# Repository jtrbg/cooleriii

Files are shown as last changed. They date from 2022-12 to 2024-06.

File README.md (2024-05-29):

# cooler iii

An application that is used to control the CoolerCoolerCooler

## Current Issues
1. **Weight**
   - The weight of the current prototype is too heavy for the current motor (even without a loaded cooler). The motor and/or overall weight of the build needs to be optimized.

2. **Precision and Strength of Printed Parts**
   - While the printed motor hub connecting the wheel and the motors originally broke from the stress (`orig_motor_hub.stl`), the new design does not break, but the mounting holes bend causing tilt in the wheels (`new_motor_hub.stl`).

3. **Functionality**
   - **Axis Module:** Did not provide accurate readings of direction even when tilt was disregarded (level surface).
   - **Bluetooth and Application:** While the custom application could read from the module, it would not 'write' proper instructions to the device. With that, we were able to determine the location of both the phone and the device, but unable to properly communicate/decode instructions from the app.

## GUIDE TO USE
## Main Application

The main app features two screens which the user can swipe between 
- Automatic Screen
  - This screen features a map that pins both the user's location and the cooler's location 
  - When viewing this screen, control mode will be set to automatic, allowing the cooler to follow the user
- Manual Screen
  - This screen features a controller UI that is customizable in settings
  - When viewing this screen, control mode will be set to manual, allowing the user to control the cooler
If the app has not been bonded, the user will be prompted to scan and connect to a 
CoolerCoolerCooler BT module   (OnStartup)

## Bluetooth Connectivity

To connect to the BT module of the cooler, the user will be directed to the Bluetooth Screen which
allows the user to scan, connect, and bond the cooler's BT module to the app
- Bluetooth Screen
  - This screen contains the information of the currently bonded device and an expandable menu that scans for devices
  - If a device is not connected, the app will automatically scan for new devices
  - To connect to a device, the user will simply tap on a desired device's label

## Automatic pathfinding

When a user is on the Automatic Screen and the 'Follow-Me' toggle is switched on, the cooler follows
the user's GPS signal using a determined pathfinding algorithm to navigate unseen obstacles

## Controller UI

To manually control the cooler, the user can swipe or tap to the Manual Screen and use the
wheel and slider buttons to control the coolers direction and speed

## Settings - Customizations/Modifications

Any customizations/modifications to the app or controls will be found through the settings button
at the top right of the Main Screen
- Theme
- Controller
- GPS
- Bluetooth
- Cooler

### Dependencies

- flutter_blue_plus ^1.3.1
  - startLeScan(UUID[],LeScanCallback) has been deprecated
  - stopLeScan(LeScanCallback) has been deprecated
- location ^4.4.0
  - isFromMockProvider() has been deprecated
- settings_ui ^2.0.2      (PLAN TO REMOVE)

### Permissions(On phone)

- Bluetooth
- Location
- Read and Write

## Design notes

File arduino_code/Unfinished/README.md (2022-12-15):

This folder contains code that was used to test modules and an attempt to create a serial connection to the device

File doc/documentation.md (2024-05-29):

```markdown
# Cooler Cooler Cooler Documentation

### Matthew Demchuk, Joshua Brull, Jovanni Rodriguez, Kai Xu
#### Dr. Franchi
#### COSC 451
#### Fall 2022

## Original Concept
**FollowMeCooler**  
We wanted to expand upon their idea and make it more successful in two areas: responsiveness and being able to drive the cooler on the beach (offroading).

## Chassis Design

### Materials
- ½ in x 2 ft x 4 ft Sanded Plywood
- 1-½ in x ⅝ in Inside Corner Braces
- 8 x 1-½ in Wood Screws
- 9 in Balloon Beach Wheels
- 12V 12 rpm DC Worm Gear Motor
- 8 in Caster Wheel
- ⅜ in x 1-½ in Bolts
- ⅜ in Lock Nuts
- ⅜ in Washers
- M4 x 15mm Steel Bolts
- Tupperware
- Cooler

### Dimensions
- Main Body: 14-⅛ in x 10-⅞ in x 4 in
- Caster Wheel Plate: 9-½ in x 9-⅛ in x ½ in
- Motor Mount Plates: 2-¼ in x 2 in x ½ in

### Details
- Corner Braces used on both the Motor Mount and Caster Wheel plates to help secure them to the Main Body. Though one of the Motor Mount plates corner braces screws are stripped causing it to tilt when placed on the ground.
- M4 Bolts are used to attach the Motor to the Motor Mount Plate.
- ⅜ in Bolts, Lock Nuts, and Washers used to mount the Caster Wheel to the Caster Wheel Mount Plate.
- Corner Brace Screws are sticking out in the Main Body will need to sanded down or cut off to prevent user injury.
- Both Plates will need to be redesigned if the motor or caster wheel is changed in the future.

## 3-D Motor Mount

With the current motor and wheels for the robot, the 3-D model does need to be modified. Both the bolt’s and motor shaft do not fit the holes on the mount and have required us to drill them out a bit to fit properly. These will need to be adjusted to fit both the wheel and motor properly.

## Wire Diagram

This is how the robot is currently wired up and allows the ArduinoBlue app to connect to the device. This does need to be improved as it is currently believed that there is too much power running into the Breadboard overloading the HM-10 if it is the only thing that is plugged into the board. From our understanding resistors were needed to prevent this from happening but were unable to figure out how to properly accomplish that in the device.

## Parts List
- 2 - 9” Beach Wheels
  - Works for the current iteration of the robot but moves at slow speed due to power of the motor
- 2 - 12V 12 rpm DC Worm Gear Motor
  - These need to be improved upon as the speed is very slow and the amount of power it produces is not enough to go on rugged terrain
- 1 - 8” Caster Wheel
  - Needs to be improved upon as due to the size of the wheel it would have trouble going across terrain such as sand due to its narrow design and weight causing it to sink in the sand
- 1 - Bluetooth Module HC-05 / HM-10
  - The bluetooth module connecting to the application on the phone was a time sink as searching through poorly documented libraries stopped progress at all ends. Code related to the module needs to be improved and synced with the serial or BLE services on the phone application
- 1 - GPS Module
  - The GPS module code is good to go.
- 1 - HMC5883L Axis Module
  - We aren't sure of the future 'direction'(ha) on the module. Whether it was an issue specific to the module, our code, or our applied application - this module stopped at nothing to provide inaccurate readings
- 1 - L298N Motor Driver
  - LGTM

## Application
The main issue in the app was the Bluetooth connection to the module; it stole all the time away from GUI development. Solid research on Android and iOS Bluetooth data transmission and the embedded libraries on each of these devices will likely solve any errors in this section.

## Code
Can be found on the public GitHub repository, along with the zip file submitted to Dr. Franchi.

Within the repository, you will find the application we planned to use originally but was scrapped due to issues with sending data to the HC-05 and HM-10 Bluetooth modules. Along with the Arduino code uploaded onto the Arduino Uno currently and code used to test the various modules and motors attached to the device.
```
<!-- @import "[TOC]" {cmd="toc" depthFrom=1 depthTo=6 orderedList=false} -->

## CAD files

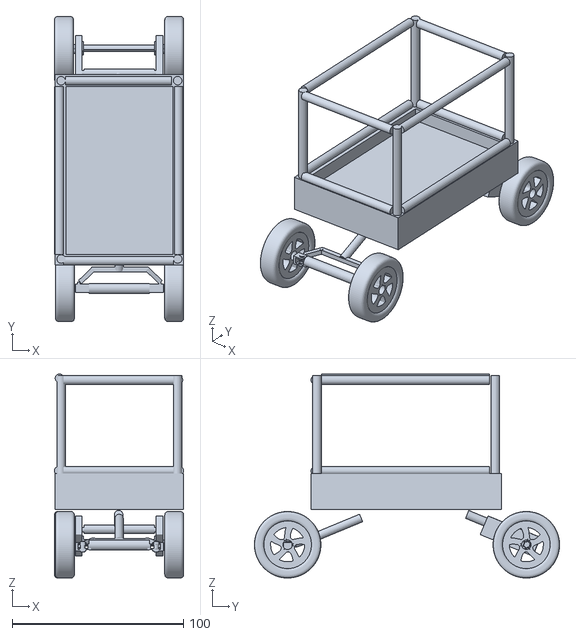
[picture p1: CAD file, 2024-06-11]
designs/new_full_build.stl
75.5 x 178.0 x 119.0

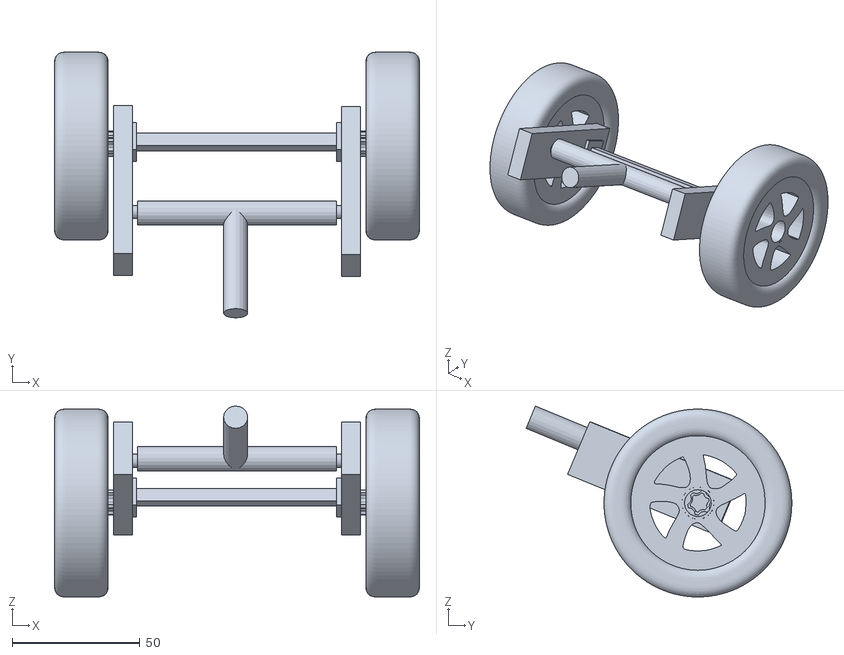
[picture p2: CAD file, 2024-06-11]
designs/new_back_wheels.stl
142.9 x 104.0 x 74.7

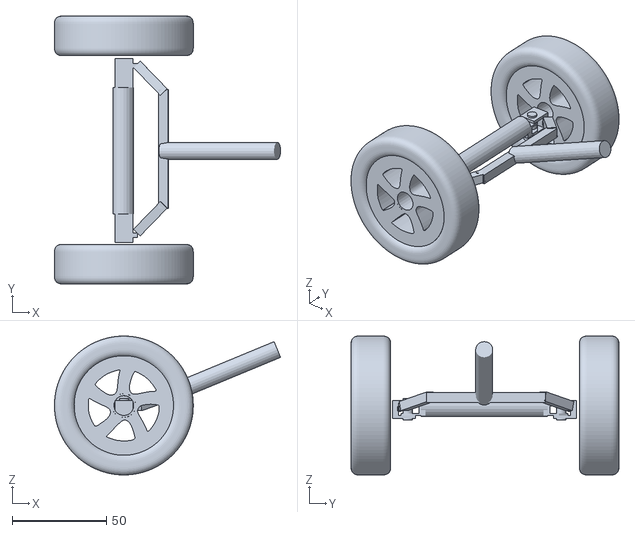
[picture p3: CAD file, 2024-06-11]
designs/new_front_wheels.stl
119.7 x 141.9 x 73.5

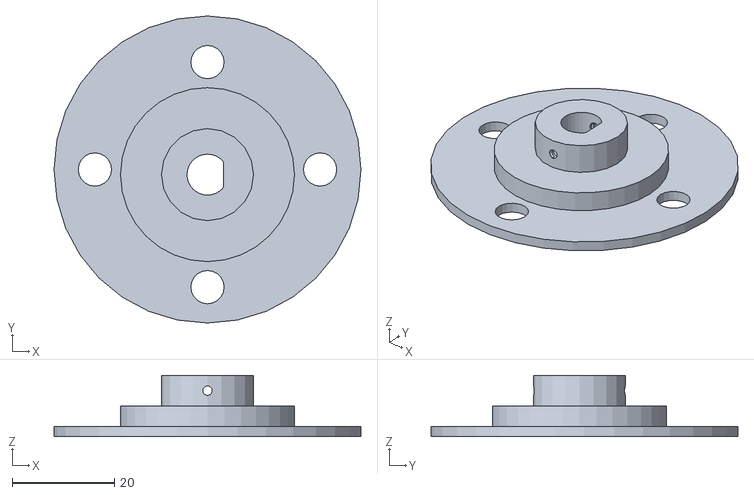
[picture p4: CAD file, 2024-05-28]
designs/orig_motor_hub.stl
60.0 x 60.0 x 12.0

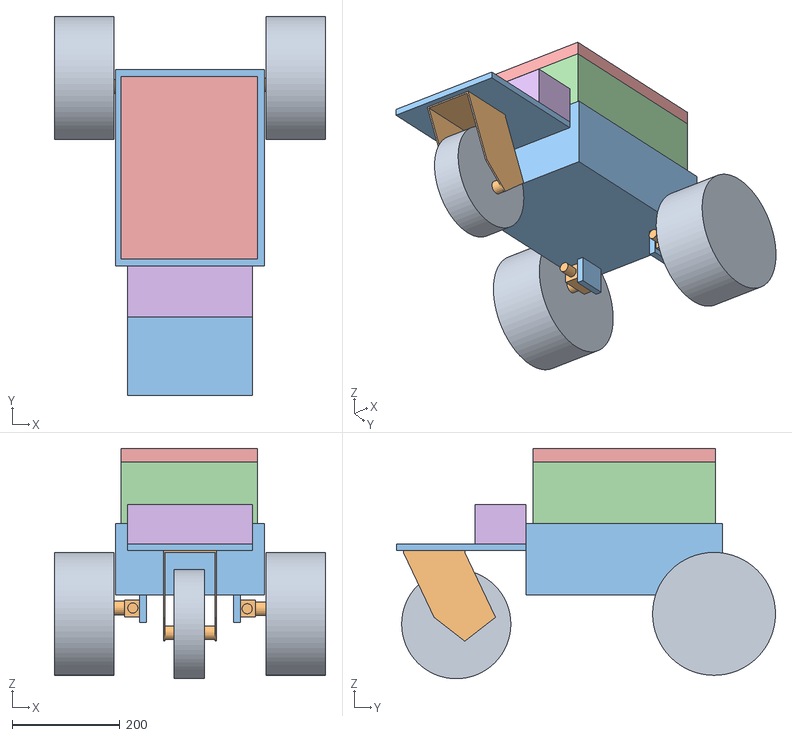
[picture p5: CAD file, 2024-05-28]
designs/build.obj
504.8 x 704.9 x 428.6

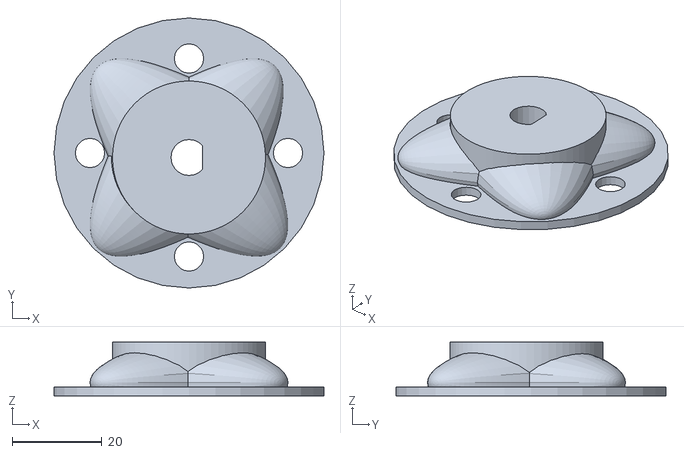
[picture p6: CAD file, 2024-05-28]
designs/new_motor_hub.stl
60.0 x 60.0 x 12.0

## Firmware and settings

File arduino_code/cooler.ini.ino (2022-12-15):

/*
ArduinoBlue-library demo for driving differential drive robot.
Instructions:
  1. Set the pin constants.
  2. Edit the motorSetForward, motorSetBackward, and motorBrake functions as necessary (see comments).
  3. Test the functions from step 2 by calling them and setting the motor speed to max (see doTesting function)
		CAUTION: The motor set functions must not set the motor speed. This function simply configures the motor controller.
  4. Uncomment controlDrive function and comment doTesting function in the loop
  5. Connect to app and drive.
 */


#include <SoftwareSerial.h> // SoftwareSerial for serial communication with HM10 bluetooth module.
#include <ArduinoBlue.h> // ArduinoBlue bluetooth library

const unsigned long BAUD_RATE = 9600;

// MOTOR LEFT PINS
const int ENA = 10;
const int IN1 = 8;
const int IN2 = 7;
// MOTOR RIGHT PINS
const int ENB = 11;
const int IN3 = 6;
const int IN4 = 9;

// MOTOR PARAMETERS
// Minimum PWM value of analogWrite to spin motor when robot is on the ground.
const int MINIMUM_MOTOR_SPEED = 0;

// HM10 BLUETOOTH MODULE PINS
// NOTE: Not all pins on your Arduino may support SoftwareSerial.
// Please check: https://www.arduino.cc/en/Reference/softwareSerial
const int BLUETOOTH_TX = 7;
const int BLUETOOTH_RX = 8;

SoftwareSerial softSerial(BLUETOOTH_TX, BLUETOOTH_RX); // Object for serial communication to HM 10 bluetooth module using ditigal pins.
ArduinoBlue phone(softSerial); // Object for smartphone robot control.

// Configures the motor controller to stop the motors.
void motorBrake() {
	digitalWrite(ENA, LOW);
	digitalWrite(ENB, LOW);
	digitalWrite(IN1, LOW);
	digitalWrite(IN2, LOW);
	digitalWrite(IN3, LOW);
	digitalWrite(IN4, LOW);
	digitalWrite(ENA, HIGH);
	digitalWrite(ENB, HIGH);
	// Do not write the motor speeds on this function. It simply configures the motor controller.
}

// Configures the motor controller to have the robot move forward.
void motorSetForward() {
	digitalWrite(IN1, LOW);
	digitalWrite(IN2, HIGH);
	digitalWrite(IN3, LOW);
	digitalWrite(IN4, HIGH);
	// Do not write the motor speeds on this function. It simply configures the motor controller.
}

// Configures the motor controller to have the robot move backwards.
void motorSetBackward() {
	digitalWrite(IN1, HIGH);
	digitalWrite(IN2, LOW);
	digitalWrite(IN3, HIGH);
	digitalWrite(IN4, LOW);
	// Do not write the motor speeds on this function. It simply configures the motor controller.
}

void setPins() {
	// Set pins as input or output
	pinMode(ENA, OUTPUT);
	pinMode(IN1, OUTPUT);
	pinMode(IN2, OUTPUT);
	pinMode(ENB, OUTPUT);
	pinMode(IN3, OUTPUT);
	pinMode(IN4, OUTPUT);
}

void controlDrive() {
	// THROTTLE AND STEERING CONTROL
	// throttle values after subtracting 49:
	//     50 = max forward throttle
	//     0 = no throttole
	//     -49 = max reverse throttle
	// steering values after subtracting 49:
	//     50 = max right
	//     0 = straight
	//     -49 = max left
	int throttle = phone.getThrottle() - 49;
	int steering = phone.getSteering() - 49;

	if (throttle == 0) {
		// If throttle is zero, don't move.
		motorBrake();
		return;
	}

	// Determine forwards or backwards.
	if (throttle > 0) {
		// Forward
		motorSetForward();
	}
	else {
		// Backward
		motorSetBackward();
	}

	// Map throttle to PWM range.
	int mappedSpeed = map(abs(throttle), 0, 50, MINIMUM_MOTOR_SPEED, 255);
	// Map steering to PWM range.
	int reducedSpeed = map(abs(steering), 0, 50, mappedSpeed, MINIMUM_MOTOR_SPEED);

	int leftMotorSpeed, rightMotorSpeed;
	if (steering > 0) {
		// Turn Right: reduce right motor speed
		leftMotorSpeed = mappedSpeed;
		rightMotorSpeed = reducedSpeed;
	}
	else {
		// Turn Left: reduce left motor speed
		leftMotorSpeed = reducedSpeed;
		rightMotorSpeed = mappedSpeed;
	}

	// Set motor speeds
	analogWrite(ENA, leftMotorSpeed);
	analogWrite(ENB, rightMotorSpeed);

	// Print Debug Info
	Serial.print("throttle: "); Serial.print(throttle);
	Serial.print("\tsteering: "); Serial.print(steering);
	Serial.print("\tmappedSpeed: "); Serial.print(mappedSpeed);
	Serial.print("\treducedSpeed: "); Serial.print(reducedSpeed);
	Serial.print("\tleftMotorSpeed: "); Serial.print(leftMotorSpeed);
	Serial.print("\trightMotorSpeed: "); Serial.println(rightMotorSpeed);
}

void doTesting() {
	// Uncomment to test.
	// motorSetForward();
	// motorSetBackward();
	// motorBrake();

	// Set motor speeds to max
	analogWrite(ENA, 255);
	analogWrite(ENB, 255);
}

void setup() {
	delay(500);
        // Start serial communications.
        // The baud rate must be the same for both serials.
	// Start communication with HM10 bluetooth module.
	softSerial.begin(BAUD_RATE);

	// Begin serial communication with computer.
	Serial.begin(BAUD_RATE);

	// Set pin modes
	setPins();

	Serial.println("SETUP COMPLETE");
}

void loop() {
	// Refer to comment on top for step by step instructions.
	doTesting(); // Comment this after testing.
	// controlDrive(); // Uncomment this after testing.
}

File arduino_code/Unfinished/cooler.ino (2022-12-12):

#include <HMC5883L.h>
#include <Arduino.h>
#include <Wire.h>

// gemoetric constants
#define GPSERROR = 0.1;
//#define DECLINATION = -0.19926; //rad
//#define RADTODEG 57.2958;
//#define DEGTORAD = 0.017453;
//#define address 0x1E //0011110b, I2C 7bit address of HMC5883

// Motor A connections
int enA = 10;
int in1 = 8;
int in2 = 7;
// Motor B connections
int enB = 11;
int in3 = 6;
int in4 = 9;

// movement functions
void driveForward();
void driveReverse();
void turnLeft();
void turnRight();
void stop();

/*
//calculate needed turning angle 
float calcTurnAngle(float dLat, float dLong, float currOrientation);

// adjust orientation of the robot to face new point
void adjustOrientation(float currOrientation, float newOrientation);

// temp function so the code will compile
float getOrientation();

HMC5883L compass;
*/
int error = 0;

void setup() {
  /*
  // set up HMC388L (axis module)
  Serial.begin(9600);
  Wire.begin();
  Wire.beginTransmission(address);
  //Wire.write(0x02);
  //Wire.write(0x00);
  Wire.endTransmission();
*/

  // set up the motor driver
	// Set all the motor control pins to outputs
	pinMode(enA, OUTPUT);
	pinMode(enB, OUTPUT);
	pinMode(in1, OUTPUT);
	pinMode(in2, OUTPUT);
	pinMode(in3, OUTPUT);
	pinMode(in4, OUTPUT);
	
  // works for moving both motors forward
	digitalWrite(in1, LOW);
	digitalWrite(in2, LOW);
	digitalWrite(in3, LOW);
	digitalWrite(in4, LOW);
   
  // get the motors going
  analogWrite(enA, 255);
  analogWrite(enB, 255);
  Serial.begin(115200); // initialize serial for control & debugging
  stop();
}

// main loop
void loop() {

  char in_char = Serial.read();
		if (in_char=='q' || in_char=='l' || in_char=='c'){ // inputs for left turns
			turnLeft();
		}
		else if(in_char=='e' || in_char=='z' || in_char=='r'){ // inputs for right turns
			turnRight();
		}
		else if(in_char=='b'){ // backwards
			driveReverse();
		}
		else if(in_char=='f'){ // forwards
			driveForward();
		}
		else if(in_char=='s'){ // stops
		stop();
		}
  /*
  if(input == 'f'){
    driveForward();
  }
  else if(input == 'l'){
    turnLeft();
  }
  else if(input == 'r'){
    turnRight();
  }
  else if(input == 'b'){
    driveReverse();
  }
  */
/*
  int x, y, z;
  //int xmin, xmax, ymin, ymax, zmin, zmax;
  //xmin =0; xmax=0; ymin=0; ymax=0; zmin=0; zmax=0;
  Wire.write(0x03);
  Wire.endTransmission();

  Wire.requestFrom(address, 6);
  if (6 <= Wire.available()){
    x = Wire.read()<<8;
    x |= Wire.read();
    z = Wire.read()<<8;
    z |= Wire.read();
    y = Wire.read();
    y |= Wire.read();
  }
  Serial.print(" x: ");
  Serial.print(x);
  Serial.print(" y: ");
  Serial.print(y);
  Serial.print(" z: ");
  Serial.print(z);
  Serial.println();

  //driveForward();
  delay(1000);
  */
}

// sets the motors to drive forward
void driveForward() {
	digitalWrite(in1, LOW);
	digitalWrite(in2, HIGH);
	digitalWrite(in3, LOW);
	digitalWrite(in4, HIGH);
}

void driveReverse(){
  digitalWrite(in1, HIGH);
	digitalWrite(in2, LOW);
	digitalWrite(in3, HIGH);
	digitalWrite(in4, LOW);
}

// sets the motors to turn to the left
void turnLeft() {
  digitalWrite(in1, HIGH);
  digitalWrite(in2, LOW);
  digitalWrite(in3, LOW);
  digitalWrite(in4, HIGH);
}

// sets the motors to turn to the right
void turnRight() {
  digitalWrite(in1, LOW);
  digitalWrite(in2, HIGH);
  digitalWrite(in3, HIGH);
  digitalWrite(in4, LOW);
}

void stop(){
  digitalWrite(in1, LOW);
  digitalWrite(in2, LOW);
  digitalWrite(in3, LOW);
  digitalWrite(in4, LOW);
}
/*
// calculate the required turning angle
float calculateTurnAngle(float dLat, float dLong, float currOrientation) {
  float thetaP = 0.0;

  // calculate the new turning angle
  if (currOrientation >= 0 && currOrientation <= 180) {
    // base formula for calculating theta prime
    thetaP = atan(dLat / dLong - currOrientation);

    // subtract 180 from theta prime is delta latitude is < 0
    if (dLat < 0)
      thetaP -= 180;
  }
  // calculate theta prime if vehicle is facing different orientation
  else if(currOrientation > 180 && currOrientation <= 360) {
    thetaP = atan((dLat / dLong) - currOrientation  + 360);
  }
  return thetaP;
}

/*
// this function might need to swap turn left/right
void adjustOrientation(float currOrientation, float newOrientation) {
  while (currOrientation != newOrientation) {
    if (currOrientation < newOrientation) {
      turnLeft();
    }
    else if (currOrientation > newOrientation) {
      turnRight();
    }
    currOrientation = getOrientation();
  }
}

// get orientation in terms of degrees from North
float getOrientation(){
  int x, y, z;
  int xmin, xmax, ymin, ymax, zmin, zmax;
  xmin=0;xmax=0;ymax=0;ymin=0;zmin=0;zmax=0;

  Wire.requestFrom(address, 6);
  if (6 <= Wire.available()){
    x = Wire.read()<<8;
    x |= Wire.read();
    z = Wire.read()<<8;
    z |= Wire.read();
    y = Wire.read();
    y |= Wire.read();
  }
}
*/

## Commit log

2024-05-28 Added documentation on project specifications and designs.
    [build.obj, new_motor_hub.stl, orig_motor_hub.stl]
2024-05-29 Did some calculations and research on motors
    Evaluated the following motors and gearboxes for 2 and 4 motor implementations:
    - Pololu 37D Metal Gearmotor:
    - Voltage: 12V
    - No-load speed: 200 RPM
    - Stall torque: 2.06 Nm
    - Cost: ~.95
    - BaneBots RS775 18V Motor with P60 Gearbox:
    - Voltage: 18V
    - No-load speed: 19500 RPM
    - Stall Torque: 1.172 Nm
    - Cost: ~.95
    - 775 Size DC Geared Motor from RobotShop:
    - Voltage: 12V
    - No-load speed: 555 RPM
    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
2024-06-11 Design Changes
    New design for the cooler holder, wheels, steering and motor housing.
    [new_back_wheels.stl, new_front_wheels.stl, new_full_build.stl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]
